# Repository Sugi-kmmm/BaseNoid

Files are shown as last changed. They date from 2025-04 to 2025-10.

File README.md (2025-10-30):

# ヒューマノイド開発プラットフォーム BaseNoid
## What's BaseNoid
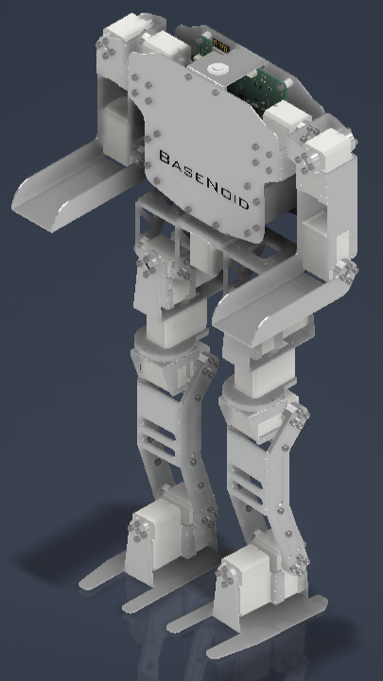
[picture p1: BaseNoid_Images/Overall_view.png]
BaseNoid_Overall_view


　BaseNoidは，低価格で本格的なヒューマノイドロボットを開発することを目的とした，ヒューマノイド開発プラットフォームです．[東京工業大学　ロボット技術研究会](https://rogiken.org/)が所持する工作機械（CNCフライス・3Dプリンタ）のみで作成できる上，必要な機械要素の入手性もきわめて高いことが特徴です．

## ファイル構成
　このリポジトリ内のファイル構成は，以下のようになっています．
```
Top
|-LICENSE                                   ライセンス情報
|-README.md                                 本リポジトリの説明
|-BaseNoid.stp                              BaseNoidの組み立て済みCADファイル
|-BaseNoid_Images           
|   |-Overall_view.png                      BaseNoidの全体図
|
|-Making_Files                              製作に必要な展開済み板金モデル等
    |-Files_for_3DP                         3Dプリンタにより作成可能なパーツ類
    |   |-Torso                             Torso部分に必要なパーツ
    |   |   |-Torso_3Dprint_parts.stp 
    |   |-Leg
    |       |-Leg_3Dprint_parts.stp         Leg部分に必要なパーツ
    |
    |-Files_for_CNC_parts                   CNCフライスにより作成可能なパーツ類（部位ごとに分類）
    |   |-Arm                               Arm部分に必要なパーツ群
    |   |   |-Arm_t1.5_CAM.stp              t1.5板材から切削可能なパーツ群
    |   |   |-Arm_t3_CAM.stp                t3板材から切削可能なパーツ群
    |   |
    |   |-Leg
    |   |   |-Leg_t1.5_CAM_1.stp            t1.5板材から切削可能なパーツ群
    |   
    |       ～略～
    |
    |-Files_for_CNC_all                     CNCフライスにより作成可能なパーツ類（部位ごとの分類なし．最大200x400の板材から削りだすことを想定）
        |-Arm_Leg_Torso_Waist_t1.5_CAM.stp  Arm,Leg,Torso,Waistに使用されるt1.5パーツ群
        |-Arm_Leg_Waist_t3_CAM.stp          Arm,Leg,Waistに使用されるt3パーツ群（t2.8パーツ含む）
        |-Leg_t1.5_CAM_1.stp                Legに使用されるt1.5パーツ群
        |           
        |           ～略～
```

## 購入部品・材料
機械要素として，以下のものを購入してください．

### [MISUMI](https://jp.misumi-ec.com/)より購入

|型番|単価|個数|小計（税別）|詳細|
| --- | --- | --- | --- | --- |
| LFW-2215 | 294円 | 3 | 882円 | スラストワッシャ．スラスト摩擦を低減する部品． |
| 80F-0403 | 60円 | 4 | 240円 | フランジ付きブッシュ．ベアリングみたいなもの． |
| PSFHRW5-42.5-MD3-ND3 | 850円 | 2 | 1700円 | 両端に目ねじがついてる棒．自分で旋盤加工して作ってOK． |
| BOB-M3-2-3W | 18円 | 52 | 936円 | クレンチングナット．板に圧入する便利なナット |

### [秋月電子通商](https://akizukidenshi.com/catalog/default.aspx)より購入

|内容|単価|個数|小計（税込）|詳細|
| --- | --- | --- | --- | --- |
| FEETECHサーボ STS3215 | 2980円 | 19 | 56620円 | シリアルサーボモータ．よくあるPWMサーボとは違って，角度とか速度とか温度とかを返してくれる，賢いサーボ |

また，必要なアルミ材は以下の通りです．（Files_for_CNC_allを用いて製作した場合）

### [井田商店](https://www.idasyouten.jp/)より購入
|内容|単価|個数|小計（税別）|詳細|
| --- | --- | --- | --- | --- |
| A5052材 t1 | 280円 | 1 | 280円 | 幅40mm 長さ40mm |
| A5052材 t1.5 | 890円 | 3 | 2670円 | 幅200mm 長さ400mm |
| A5052材 t2 | 890円 | 1 | 890円 | 幅200mm 長さ350mm |
| A5052材 t3 | 670円 | 1 | 670円 | 幅200mm 長さ170mm |
| A5052材 t5 | 210円 | 1 | 210円 | 幅120mm 長さ50mm |

合計金額（税込）：**65946**円

## ACT_Base_Circuitについて
　BaseNoidでは，制御用基板としてACT_Base_Circuit（以下，ABC）というロボット技術研究会ACTで開発している多軸ロボット向け制御基板を用いています．
　ABCリポジトリは[こちら](https://github.com/TokyoTech-SSR-ACT/ACT_Base_Circuit)です．
　※現在，ABCはβ版の状態です．ご了承ください．

　ABCを使用しない場合は，[秋月電子通商様のSTS3215商品ページ](https://akizukidenshi.com/catalog/g/g116312/)内で紹介されている[参考資料](https://akizukidenshi.com/goodsaffix/feetech_digital_servo_20220729.pdf)の7ページ目をご確認の上，ご自分で回路を実装していただけましたら幸いです．

## iptファイルについて
　BaseNoidは，Autodesk Inventor Professional 2026にて開発されています．
 
　Inventor形式のファイルが必要な方は，[開発者HP内のコンタクトに記載された手段](https://sugi-kmmm.github.io/contact.html)nいよりお問い合わせください．

## コンタクト
　技術的お問い合わせは，本リポジトリのIssueよりお願いいたします．

　その他の問い合わせについては，[開発者HP内のコンタクトに記載された手段](https://sugi-kmmm.github.io/contact.html)により行ってください．また，教育機関の講義で使用する場合等においては，特段の連絡は必要ありませんが，ご報告していただけますと製作者のモチベーションにつながります．ぜひご一報いただけますと幸いです．

## LICENSE情報
BaseNoidは以下のクリエイティブ・コモンズ・ライセンスにより保護されています．

BaseNoid © 2025 by [Rei Sugihara](https://sugi-kmmm.github.io/index.html) is licensed under [CC BY-NC-SA 4.0](https://creativecommons.org/licenses/by-nc-sa/4.0/?ref=chooser-v1).

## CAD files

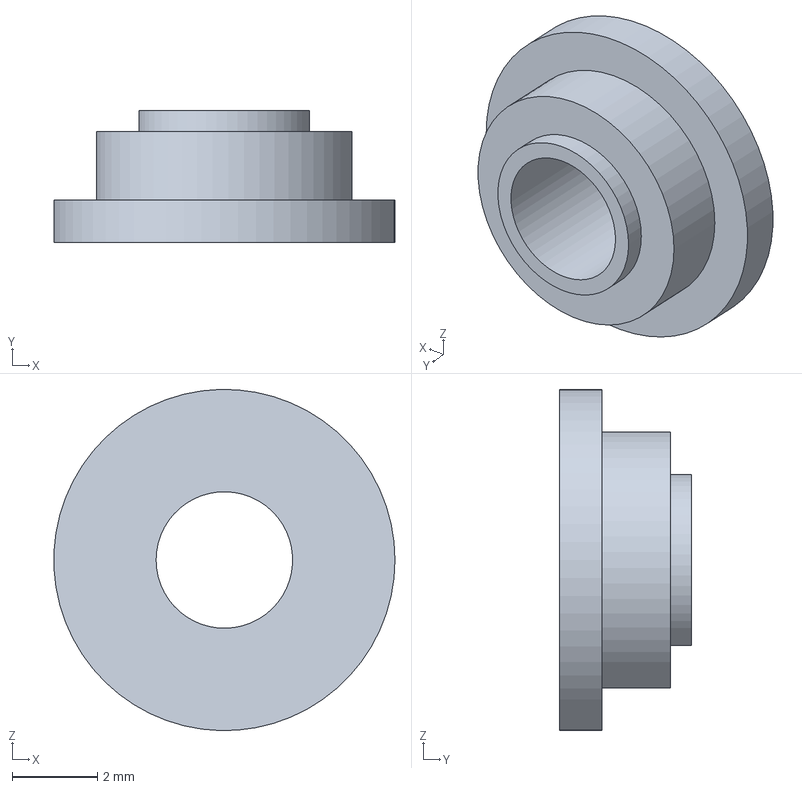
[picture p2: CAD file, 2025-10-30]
Making_Files/Files_for_3DP/Leg/Leg_3Dprint_parts.stp
7.99 x 3.10 x 8.00 mm

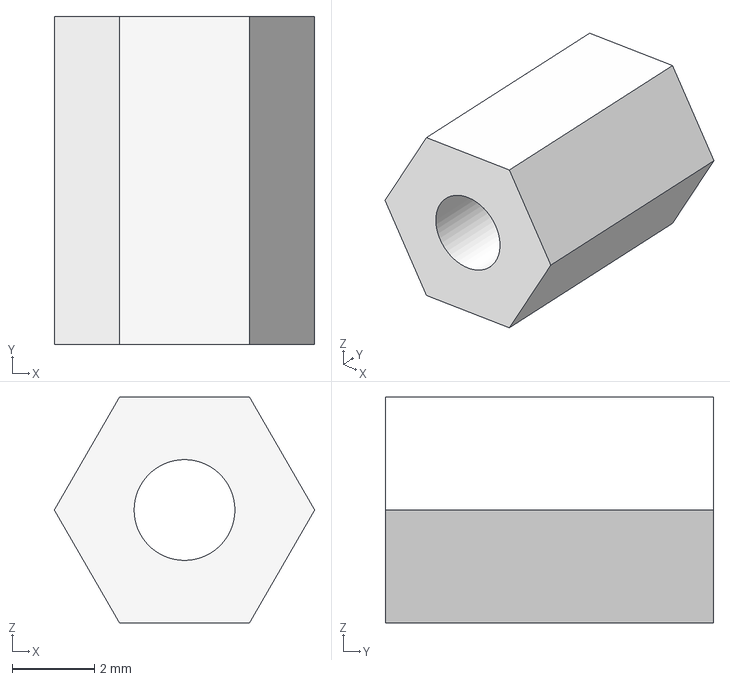
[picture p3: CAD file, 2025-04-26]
Making_Files/Files_for_3DP/Torso/Torso_3Dprint_parts.stp
6.35 x 8.00 x 5.50 mm

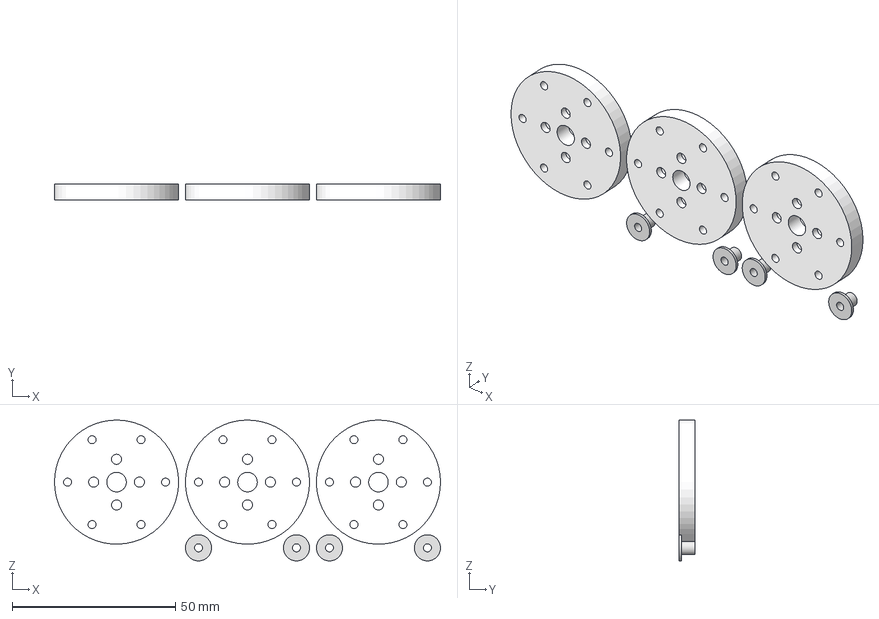
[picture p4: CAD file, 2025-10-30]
Making_Files/Files_for_CNC_all/Leg_Waist_t5_CAM.stp
118.2 x 5.00 x 43.1 mm
roll_free_horn_axis_2 x 4
waist_spacer

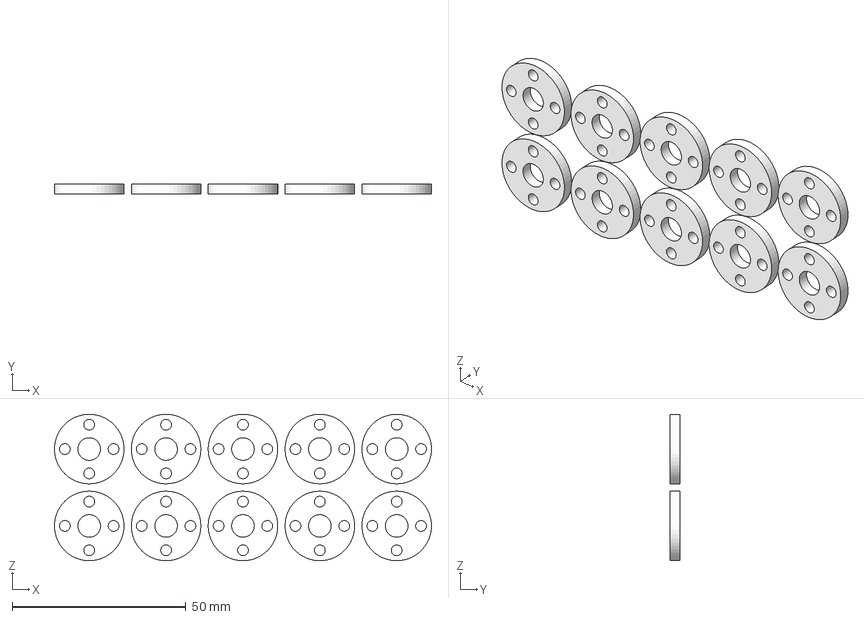
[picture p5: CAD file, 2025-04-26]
Making_Files/Files_for_CNC_parts/Arm/Arm_t3_CAM.stp
108.4 x 3.00 x 42.1 mm
servo_horn_spacer x 10

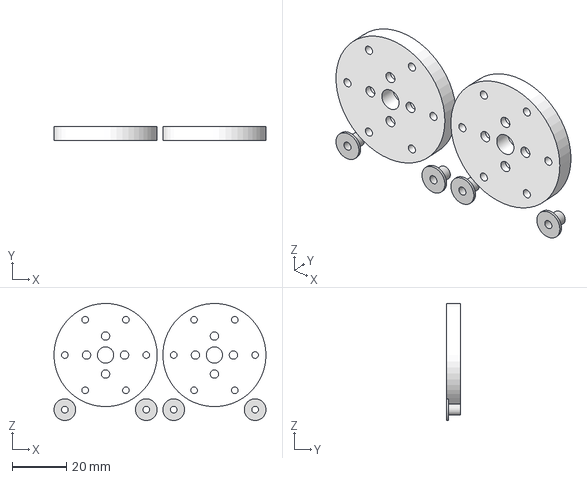
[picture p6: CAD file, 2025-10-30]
Making_Files/Files_for_CNC_parts/Leg/Leg_t5_CAM.stp
78.1 x 5.00 x 43.1 mm
roll_free_horn_axis_2 x 4

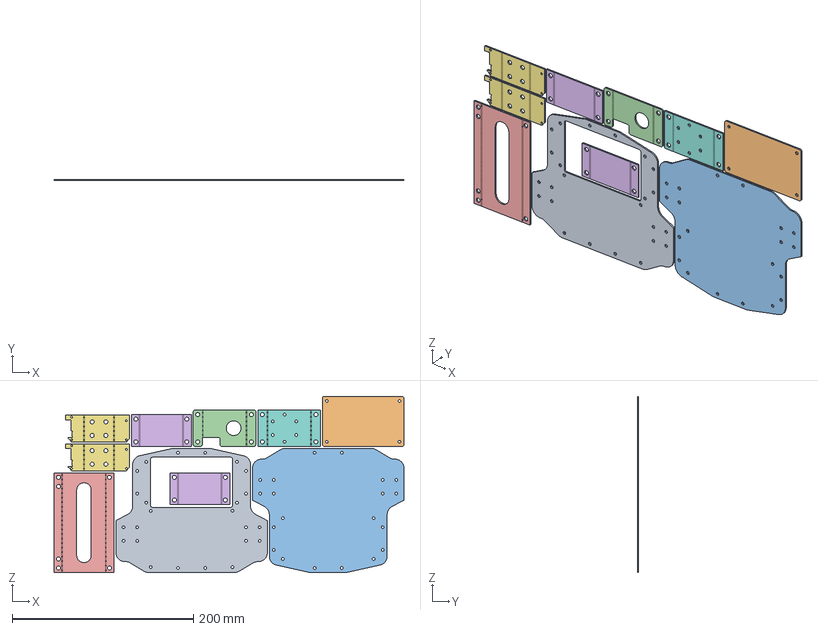
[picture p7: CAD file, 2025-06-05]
Making_Files/Files_for_CNC_parts/Torso/Torso_t1.5_CAM_1.stp
385.8 x 1.50 x 194.1 mm
back_pannel
battery_cover
front_pannel
Under_torso
Li-Po_cover_1
Li-Po_cover_2 x 2
shoulder_base_1
shoulder_base_2
Under_torso_1

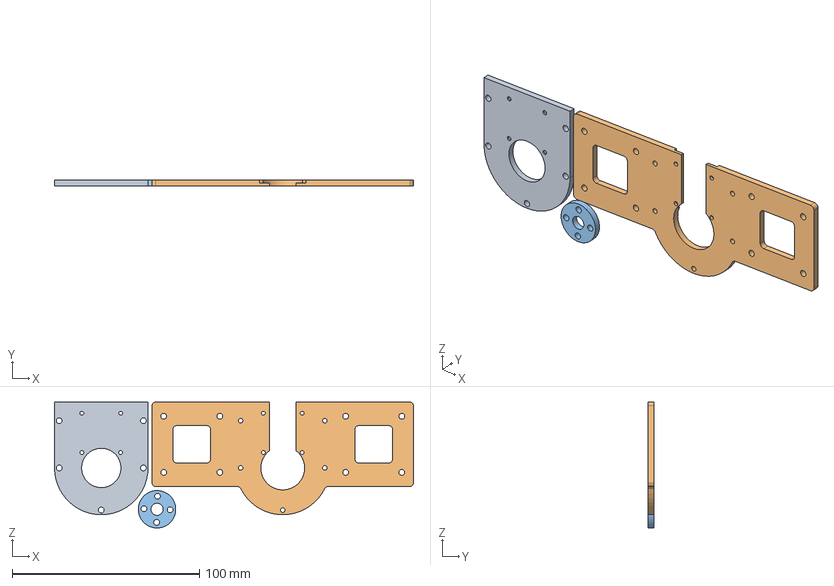
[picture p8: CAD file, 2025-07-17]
Making_Files/Files_for_CNC_parts/Waist/Waist_t3_CAM.stp
191.8 x 3.00 x 67.3 mm
waist_2
waist
servo_horn_spacer

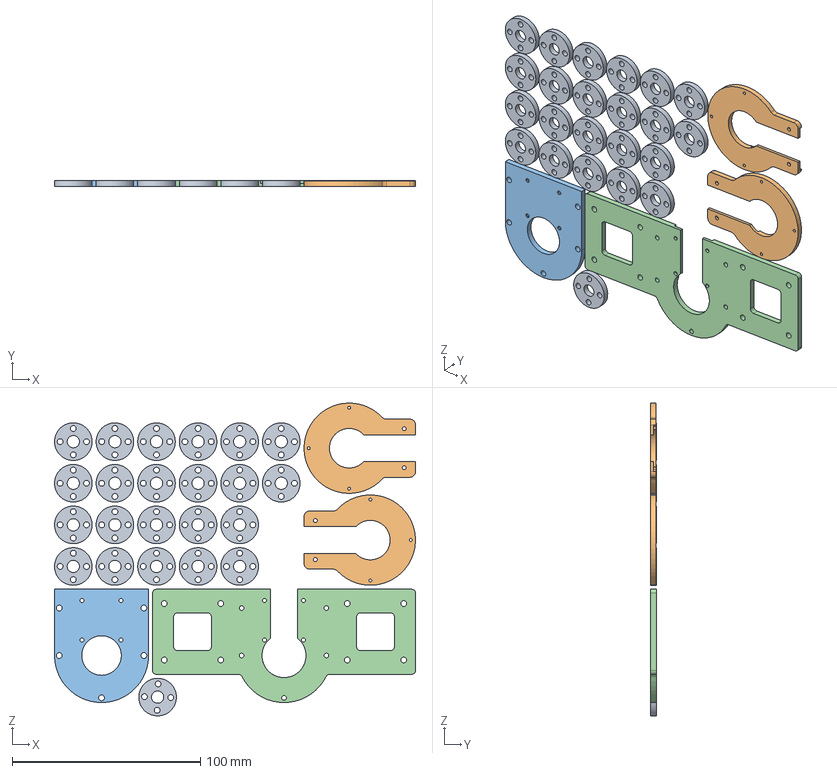
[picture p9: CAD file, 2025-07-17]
Making_Files/Files_for_CNC_all/Arm_Leg_Waist_t3_CAM.stp
191.8 x 3.00 x 166.2 mm
servo_horn_spacer x 10
hip_joint_yaw_spacer_2 x 2
servo_horn_spacer_1 x 12
waist_2
waist
servo_horn_spacer_2

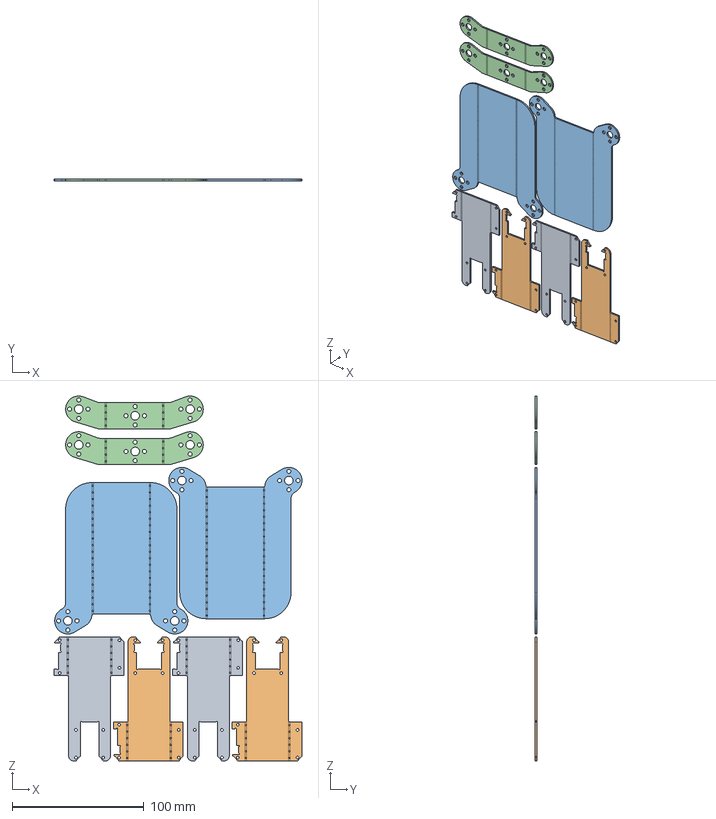
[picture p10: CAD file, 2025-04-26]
Making_Files/Files_for_CNC_parts/Arm/Arm_t1.5_CAM.stp
188.4 x 1.50 x 277.2 mm
Upper_arm_1 x 2
Upper_arm_2 x 2
Fore_arm_1 x 2
Shoulder_joint_1 x 2

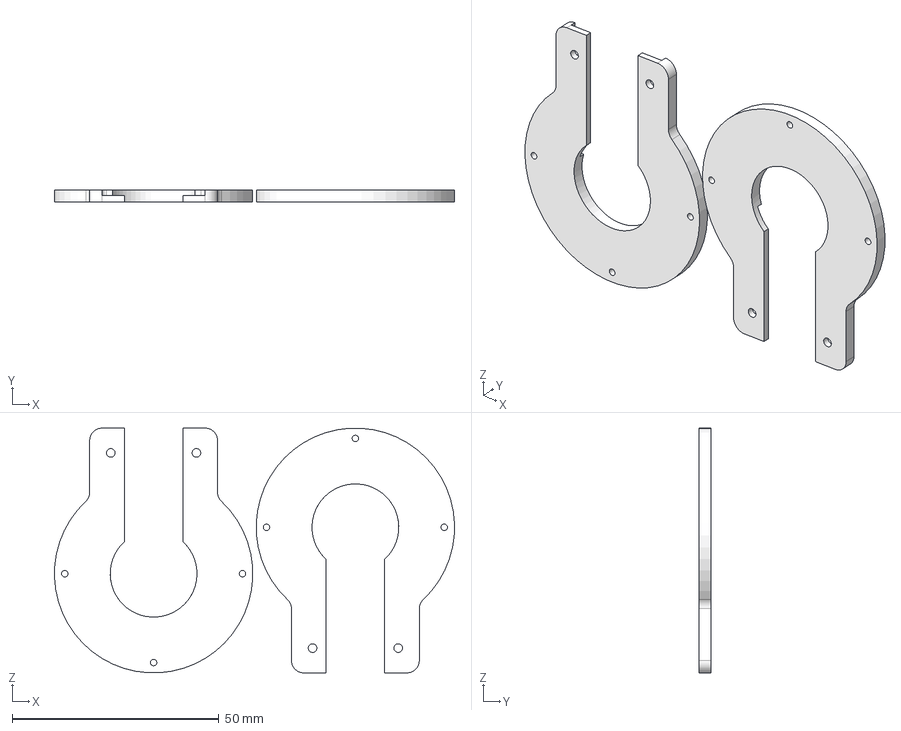
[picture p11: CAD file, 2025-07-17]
Making_Files/Files_for_CNC_parts/Leg/Leg_t2.8_CAM.stp
96.8 x 2.80 x 59.2 mm
hip_joint_yaw_spacer_2 x 2

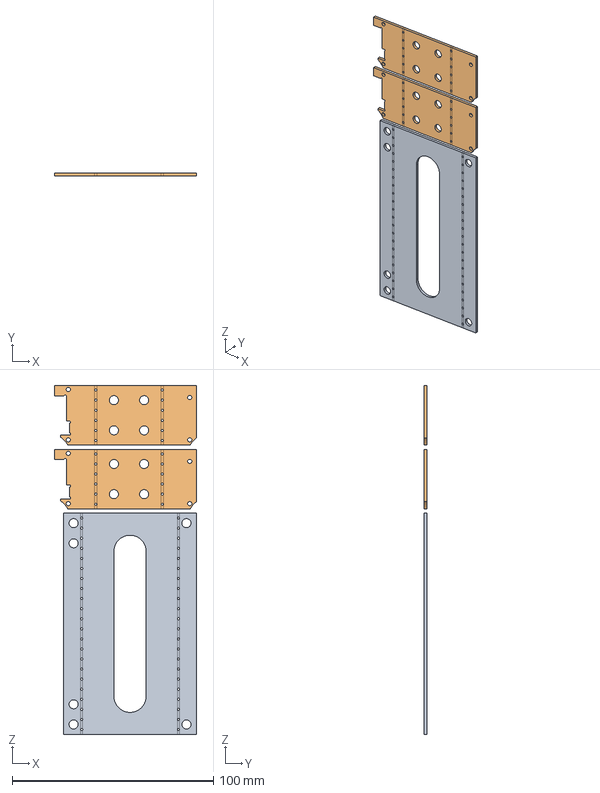
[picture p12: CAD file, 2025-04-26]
Making_Files/Files_for_CNC_parts/Torso/Torso_t1.5_CAM_2.stp
70.6 x 1.50 x 173.4 mm
Li-Po_cover_1
shoulder_base_2
shoulder_base_1

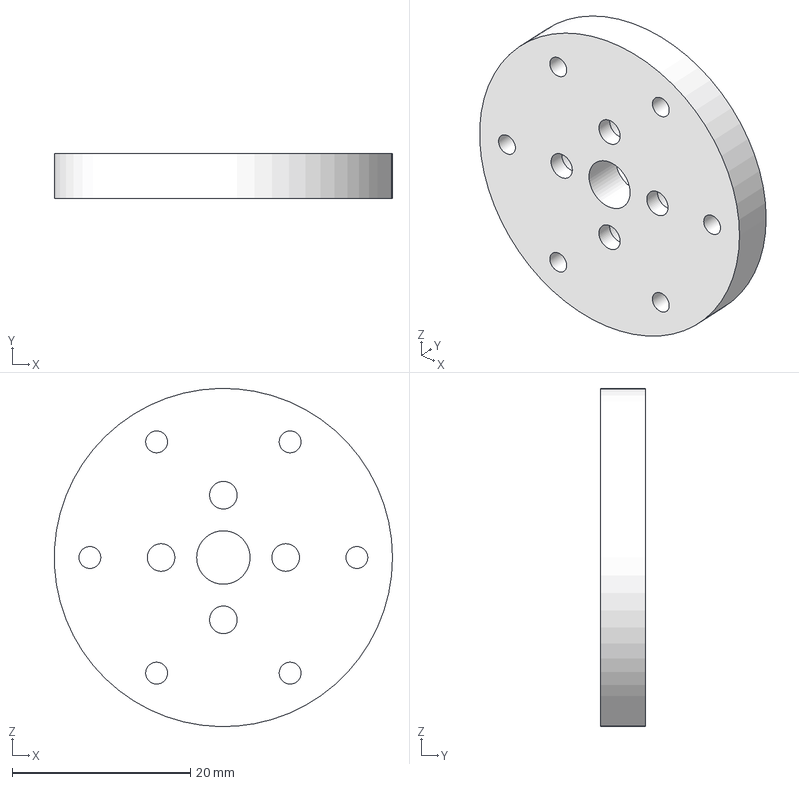
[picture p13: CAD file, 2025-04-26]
Making_Files/Files_for_CNC_parts/Waist/Waist_t5_CAM.stp
38.0 x 5.00 x 38.0 mm

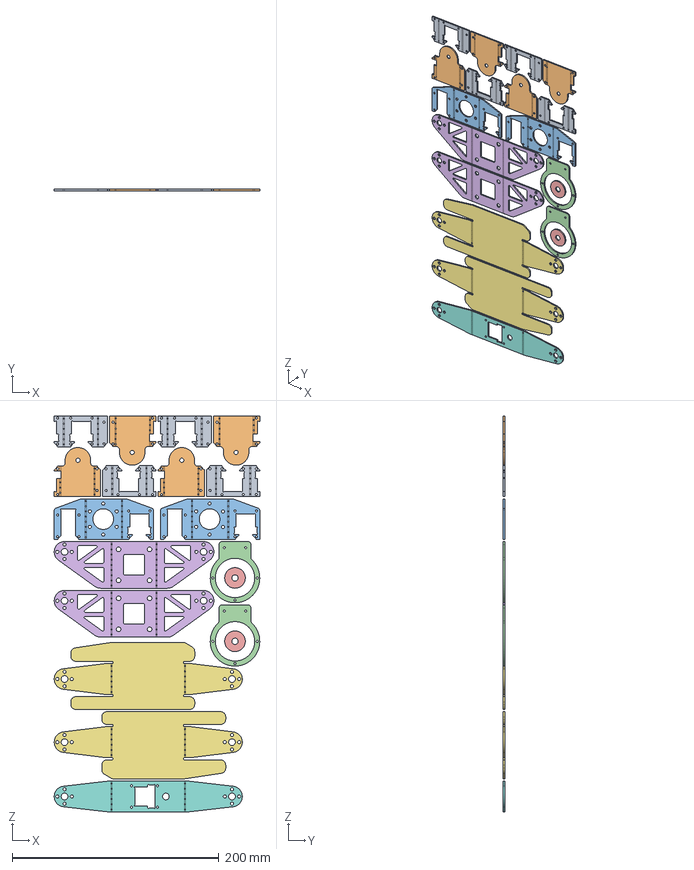
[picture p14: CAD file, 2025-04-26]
Making_Files/Files_for_CNC_parts/Leg/Leg_t1.5_CAM_1.stp
199.0 x 1.50 x 383.3 mm
roll_pitch_connecter x 4
roll_free_horn_axis x 4
knee_joint_1 x 2
hip_joint_yaw_washer_holder x 2
hip_joint_yaw_spacer x 2
hip_joint_2 x 2
ankle_joint_1 x 2
hip_joint_1

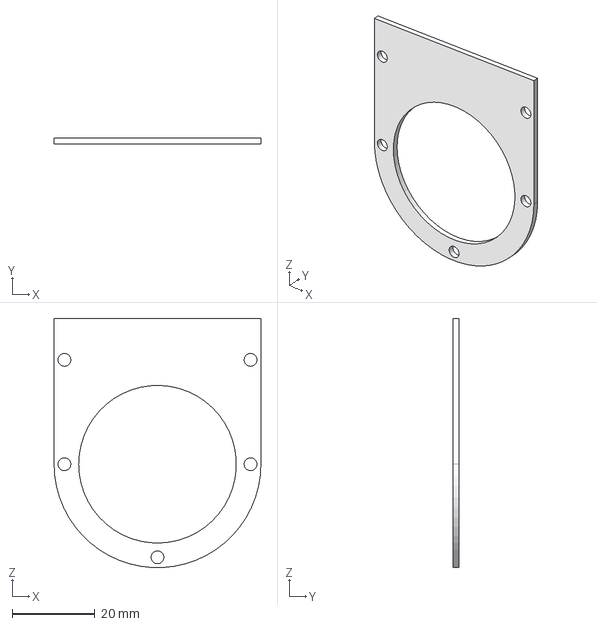
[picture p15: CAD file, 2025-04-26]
Making_Files/Files_for_CNC_parts/Waist/Waist_t1.5_CAM.stp
50.0 x 1.50 x 60.2 mm

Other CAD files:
Making_Files/Files_for_CNC_all/Arm_Leg_Torso_Waist_t1.5_CAM.stp
Making_Files/Files_for_CNC_parts/Leg/Leg_t1_CAM.stp
Making_Files/Files_for_CNC_all/Leg_t1_CAM.stp
Making_Files/Files_for_CNC_all/Leg_t2_CAM.stp
Making_Files/Files_for_CNC_parts/Leg/Leg_t1.5_CAM_2.stp
Making_Files/Files_for_CNC_parts/Leg/Leg_t2_CAM.stp
Making_Files/Files_for_CNC_parts/Leg/Leg_t3_CAM.stp

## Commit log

2025-04-26 add BaseNoid CAD File
2025-06-05 Resolve part interference
    [Torso_t1.5_CAM_1.stp]
2025-07-17 model error updated
    [Arm_Leg_Waist_t3_CAM.stp, Leg_t2.8_CAM.stp, Waist_t3_CAM.stp]
2025-10-30 Updated : Leg Free Horn Axis
    [Leg_3Dprint_parts.stp, Leg_Waist_t5_CAM.stp, Leg_t5_CAM.stp]
